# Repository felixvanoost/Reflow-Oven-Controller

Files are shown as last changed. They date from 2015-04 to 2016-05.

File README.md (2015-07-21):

Copyright Felix van Oost 2015.
This program is free software: you can redistribute it and/or modify it under the terms of the GNU General Public License as published by the Free Software Foundation, either version 3 of the License, or (at your option) any later version. This program is distributed in the hope that it will be useful, but WITHOUT ANY WARRANTY; without even the implied warranty of
MERCHANTABILITY or FITNESS FOR A PARTICULAR PURPOSE. See the GNU General Public License for more details.

# Reflow Oven Controller
A project to convert a standard toaster oven into a reflow soldering oven for PCB assembly using an Arduino and Python.

----------
Context
----------

The rapid adoption of surface-mount technology has revolutionised the electronics industry by reducing the size, cost, and power requirements of components. For the hobbyist, however, soldering these ever-smaller components by hand is becoming increasingly difficult. The most consistent and efficient way of soldering SMT components is by reflow soldering, a technique in which parts are attached to the PCB using solder paste and the entire board is then heated inside a purpose-built oven. The heat melts the solder paste, thereby permanently soldering the components to the board.

Reflow soldering requires precise control of the oven temperature, so the process is performed commercially in expensive, purpose-built reflow ovens. However, excellent results can be achieved on a budget by using a converted toaster oven and a microcontroller to monitor and adjust the temperature according to a specified thermal profile.

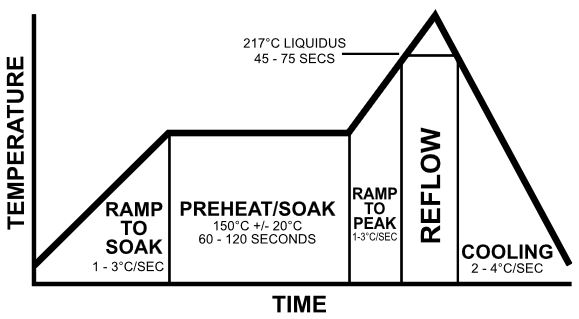
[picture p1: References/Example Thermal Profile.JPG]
Image of example thermal profile

*Example thermal profile*

The specific thermal profile followed by the microcontroller will depend on the type of solder paste and components used on the board (temperature guidelines are often provided in component datasheets). It is split into five main stages - ramp to soak, soak, ramp to reflow, reflow, and cooling. Each section dictates the specific temperature, time, and ramp up / down characteristics required for optimal soldering results. A full reflow cycle usually takes in the region of 4-6 minutes to complete.

----------
Overview
----------

This project consists of three main components:

- An off-the-shelf toaster oven fitted with a solid-state relay (SSR).
- An Arduino Uno to monitor and control the oven to follow a user-defined thermal profile.
- A Python script to provide a text-based UI for the Arduino and display a live plot of the oven temperature data on a computer.

To help keep the scope sufficiently narrow, I will assume that a suitable oven has been purchased and an SSR has already been installed within - there are a number of very good tutorials describing how to do this step-by-step. Information on choosing a suitable toaster oven for reflow soldering can be found [here](http://www.rocketscream.com/blog/2011/06/19/toaster-convection-or-infrared-oven/).

Four thermal profile parameters are user-configurable:

- Soak temperature
- Soak time
- Reflow temperature
- Reflow time

The Python script prompts the user to enter the desired values for each parameter, checks the input is within a pre-determined valid range, then sends the values to the Arduino via USB. Once the reflow cycle has been started, it receives an oven temperature reading from the Arduino every second and plots this on a graph for the user in real-time. The script also notifies the user when the cycle is complete or has been stopped for some reason.

The Arduino uses a finite state machine to implement the control logic, with a state corresponding to each stage in the reflow cycle. It controls the toaster oven using time-proportional control (a slower form of PWM). User feedback is provided via a set of LEDs and a buzzer.

----------
Hardware
----------

The hardware is split into the following main functional blocks:

- A thermocouple to measure the temperature inside the oven
- An amplifier circuit to amplify the voltage across the thermocouple to a level readable by the Arduino
- A temperature sensor to perform cold-junction compensation on the thermocouple temperature reading
- Pushbuttons to allow the user to start / stop the reflow process and implement any additional functionality
- LEDs and a buzzer to provide user feedback on the current stage in the reflow cycle

The following components are used:

- Arduino Uno or equivalent
- Arduino Proto Shield or equivalent
- K-type thermocouple wire (must be rated for at least 300C)
- Texas Instruments LM35Z Temperature Sensor
- Analog Devices OP07 Op-Amp or equivalent
- Texas Instruments LMC7660 Voltage Converter or equivalent (provides +/-5V bipolar output for the op-amp)
- Buzzer (this project uses a TDK PS1420P02CT)
- 4-Position screw terminal block
- 2x 8-DIP sockets
- 3x Pushbuttons (1 for start / stop, others for future additional functionality)
- 2x 5mm LEDs
- 2x 10µF electrolytic capacitors
- 2x 100Ω resistors
- 2x 330Ω resistors
- 3x 10kΩ resistors
- 2x 47kΩ resistors

The OP07 was chosen for its low input voltage characteristics (as the thermocouple produces an output voltage on the order of microvolts), although any op-amp with similar specifications will work just fine. The same is true for the LMC7660 - any voltage converter providing a +/-5V output from a 5V input can be used.

I decided to mount the hardware on an [OSEPP Proto Shield](http://osepp.com/products/shield-arduino-compatible/proto-shield/) (functionally identical to the [Sparkfun ProtoShield Kit](https://www.sparkfun.com/products/7914)), which comes pre-installed with a pushbutton and two LEDs. This reduces the number of components that need to be soldered to the board and simplifies the layout and assembly process. A full hardware schematic is provided in the 'Hardware' folder, and a few photos of the completed shield (one of many possible board layouts) can be found in the 'Photos' folder.

----------
Software
----------

The following software is required:

- Arduino IDE (latest version preferred)
- Python 3.4.2 (I opted to use IDLE in [WinPython](http://winpython.github.io/) 3.4.3.3 to run the Python UI script)

Further information about software / firmware setup and a detailed overview of the control logic is provided with each major release in the 'releases' section. Releases are versioned in the form vX.Y.ZZ, where X indicates a major new release, Y indicates a minor feature addition / update, and ZZ denotes a simple bug fix.

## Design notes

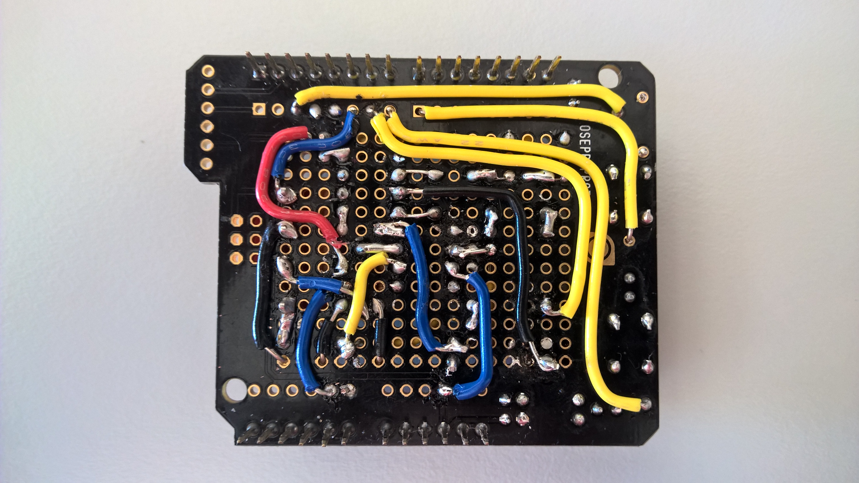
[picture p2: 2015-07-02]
Photos/Reflow Oven Controller 3.jpg

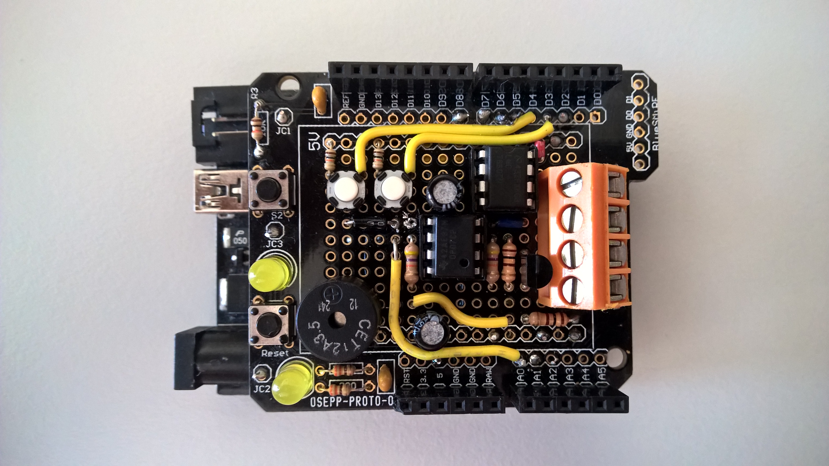
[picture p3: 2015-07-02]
Photos/Reflow Oven Controller 2.jpg

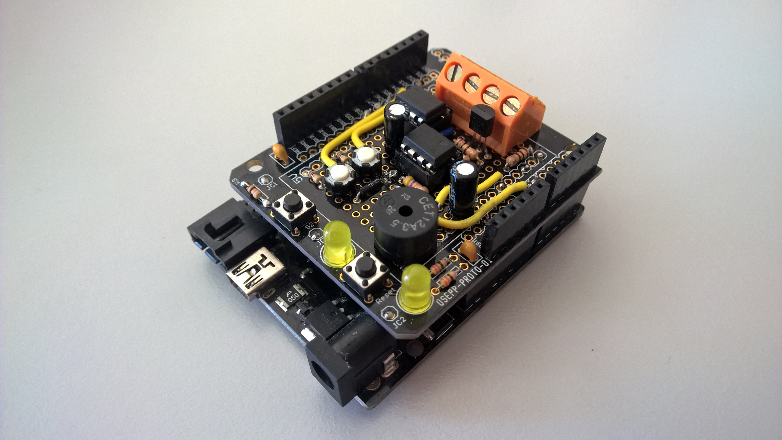
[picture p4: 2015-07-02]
Photos/Reflow Oven Controller 1.jpg

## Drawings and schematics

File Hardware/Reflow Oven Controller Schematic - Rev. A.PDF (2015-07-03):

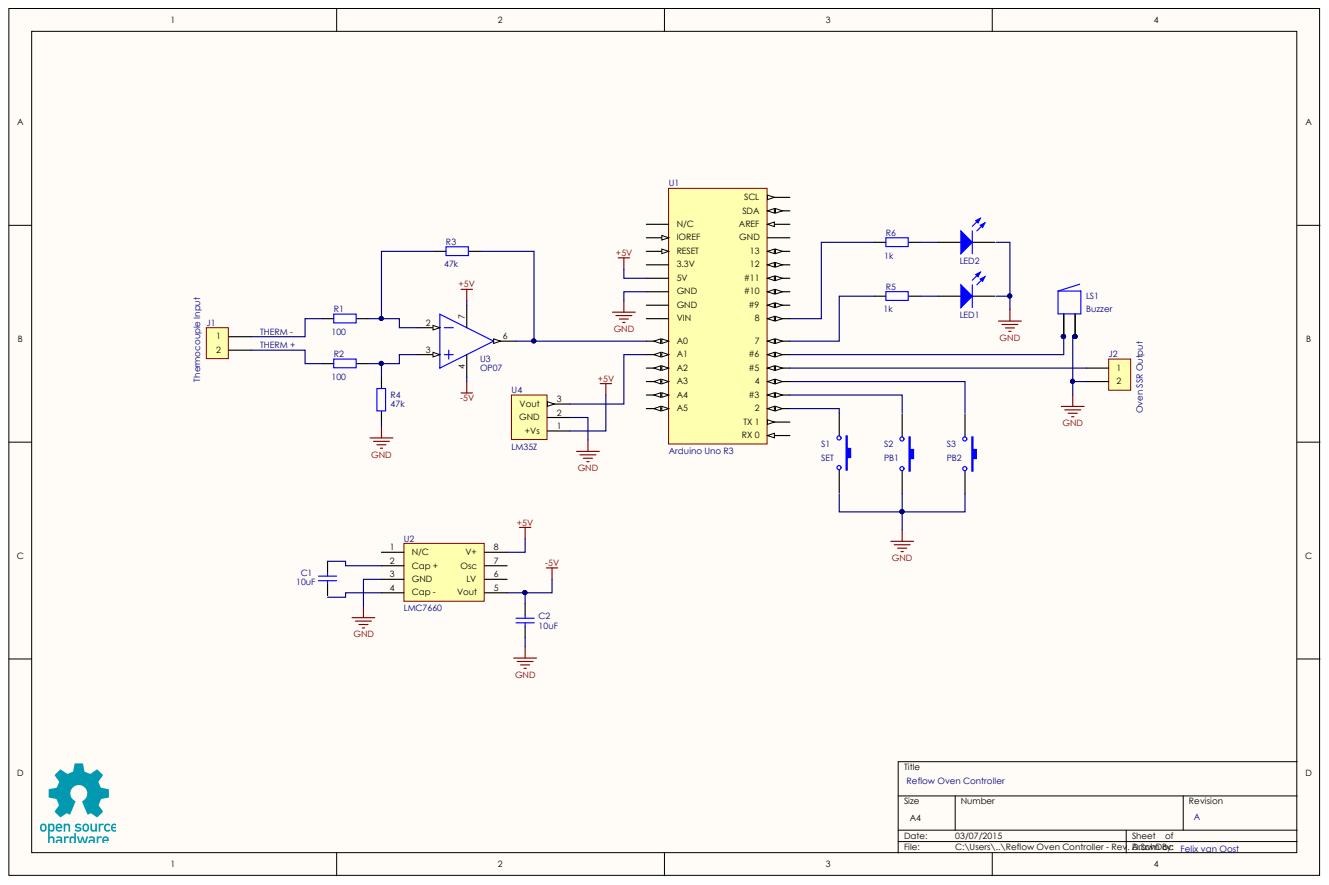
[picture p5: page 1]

S ize A4 | Num ber | Rev ision A

Date: 0 3/0 7/2 0 1 5 | Sheet of
Fi le: C :\Users\. .\Reflow Oven Control ler - Rev | . A. DraSchDoc wn By: Fel ix v an Oost

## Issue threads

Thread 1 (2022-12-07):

ISR bloated

eda1-fiunam, 2022-12-07:
I've just discovered your project, congrats! It seems very interesting, although I don't know yet whether it works, but I guess so. The first thing I've noted is that you've placed a very intensive floating point math inside the ISR. Good programming practices say that one shouldn't bloat an ISR, but delegates the user code to a regular function. I'm working on a similar project but using Fuzzy logic and a 32-bit Cortex ARM microcontroller. I'm in the design phase, and when it's time to build the electronics I'll check your project out thoroughly (I have no doubts about its performance) because it's a gold mine. Greetings.

FelixVanOost, 2022-12-09:
Hey @eda1-fiunam, thanks for getting in touch! I'm glad to hear that you found the project interesting.

I wrote this code a long time ago as a student and would do things quite differently today. You're correct in saying that ISRs should be kept as short as possible to avoid scheduling issues when multiple tasks are operating. This isn't always an issue if the ISR is the only code being executed though, or if the background code that the ISR has higher priority over doesn't need to run at a fixed period (which is somewhat true of the state machine that's running in the `loop()` function here).

In terms of execution time, the arithmetic in the ISR is trivial on any modern microcontroller with an FPU. The slowest functions are probably `Serial.print()` and the 1D look-up `pgm_read_word_near()`.

Good luck and happy hacking!

Felix

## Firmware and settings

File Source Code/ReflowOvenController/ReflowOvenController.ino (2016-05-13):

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
// Reflow Oven Controller v2.0.00

#include <avr/pgmspace.h>

// Analog pin definitions
#define thermPin                     A0                                       // Thermocouple input pin (A0)
#define junctionPin                  A1                                       // Cold junction input pin (A1)

// Digital pin definitions
#define setButtonPin                 2                                        // Pushbutton input pins (D2-D4)
#define Button1Pin                   3
#define Button2Pin                   4
#define ovenPin                      5                                        // Oven SSR pin (D5)
#define buzzerPin                    6                                        // Buzzer output pin (D6)
#define LED1Pin                      7                                        // LED output pins (D7-D8)
#define ovenLEDPin                   8

#define DEBOUNCE_DELAY               50                                       // Pushbutton debounce delay (ms)

// Buzzer frequencies (Hz)
#define LOW_BUZZER_FREQ              3000
#define MID_BUZZER_FREQ              4000
#define HIGH_BUZZER_FREQ             5000

// Buzzer beep lengths (ms)
#define SHORT_BEEP                   100
#define MEDIUM_BEEP                  400
#define LONG_BEEP                    3000

// Finite-state machine states
#define OFF                          0
#define RAMP_TO_SOAK                 1
#define SOAK                         2
#define RAMP_TO_REFLOW               3
#define REFLOW                       4
#define COOLING                      5

// PID coefficients
#define Kp                           12
#define Ki                           0
#define Kd                           3

// Oven temperature reading array size
#define READING_ARRAY_SIZE           10

// Oven temperature error array size
#define ERROR_ARRAY_SIZE             3

#define ERROR_TEMP                   35                                       // Thermocouple error temperature threshold (stops reflow process if not reached within the first 30 seconds)
#define SAFE_TO_HANDLE_TEMP          60                                       // Safe-to-handle temperature

byte state = OFF;

struct thermalProfile
{
  byte soakTemp;
  byte soakTime;
  byte reflowTemp;
  byte reflowTime;
};
typedef struct thermalProfile thermalProfile;                                 // Create a thermal profile structure
thermalProfile custom;

volatile float TargetTemp = 0;
volatile float OvenTempReading[READING_ARRAY_SIZE];
volatile float OvenTemp = 0;
volatile float OvenTempError[ERROR_ARRAY_SIZE];
volatile float TotalTempError = 0;
volatile float DeltaTemp = 0;
volatile float OvenOutput = 0;

volatile unsigned int cycleTime = 0;
volatile unsigned int stateTime = 0;

volatile byte interruptCount = 0;

// 0-255C LUT for K-type thermocouple in mV (stored in program memory)
const int thermLUT[] PROGMEM = {0,    18,   37,   56,   74,   93,   112,  130,  149,  168,
                                187,  205,  224,  243,  262,  281,  299,  318,  337,  356,
                                375,  394,  413,  432,  451,  470,  489,  508,  527,  547,
                                565,  585,  604,  623,  642,  661,  681,  700,  719,  738,
                                758,  777,  796,  815,  835,  854,  873,  893,  912,  932,
                                951,  970,  990,  1009, 1028, 1048, 1067, 1087, 1106, 1126,
                                1145, 1165, 1184, 1204, 1223, 1243, 1262, 1282, 1301, 1321,
                                1340, 1360, 1379, 1399, 1418, 1438, 1457, 1477, 1496, 1516,
                                1535, 1555, 1575, 1594, 1614, 1633, 1653, 1672, 1692, 1711,
                                1731, 1750, 1770, 1789, 1809, 1828, 1848, 1867, 1886, 1906,
                                1925, 1945, 1964, 1983, 2003, 2022, 2042, 2061, 2081, 2100,
                                2119, 2139, 2158, 2178, 2197, 2216, 2235, 2255, 2274, 2293,
                                2312, 2332, 2351, 2370, 2389, 2408, 2428, 2447, 2466, 2485,
                                2504, 2523, 2543, 2562, 2581, 2600, 2619, 2638, 2657, 2676,
                                2695, 2714, 2733, 2752, 2771, 2790, 2809, 2828, 2847, 2866,
                                2885, 2904, 2923, 2942, 2961, 2979, 2999, 3017, 3036, 3055,
                                3074, 3093, 3111, 3130, 3149, 3168, 3187, 3206, 3225, 3243,
                                3262, 3281, 3300, 3318, 3337, 3356, 3375, 3393, 3412, 3431,
                                3450, 3469, 3487, 3506, 3525, 3544, 3562, 3581, 3600, 3619,
                                3637, 3656, 3675, 3694, 3713, 3731, 3750, 3769, 3788, 3807,
                                3825, 3844, 3862, 3881, 3900, 3919, 3938, 3956, 3975, 3995,
                                4013, 4032, 4051, 4070, 4089, 4107, 4126, 4145, 4164, 4183,
                                4202, 4221, 4239, 4259, 4277, 4296, 4315, 4334, 4353, 4372,
                                4391, 4410, 4429, 4448, 4467, 4486, 4505, 4524, 4543, 4562,
                                4581, 4600, 4619, 4638, 4657, 4677, 4696, 4715, 4734, 4753,
                                4772, 4791, 4810, 4830, 4849, 4868};

void setup() 
{
  pinMode(thermPin, INPUT);
  pinMode(junctionPin, INPUT);
  pinMode(setButtonPin, INPUT_PULLUP);                                        // Enable internal pull-up resistors on pushbutton pins
  pinMode(Button1Pin, INPUT_PULLUP);
  pinMode(Button2Pin, INPUT_PULLUP);
  pinMode(ovenPin, OUTPUT);
  pinMode(buzzerPin, OUTPUT);
  pinMode(LED1Pin, OUTPUT);
  pinMode(ovenLEDPin, OUTPUT);

  // Turn LEDS off
  digitalWrite(LED1Pin, 0);
  digitalWrite(ovenLEDPin, 0);

  // Initialise oven temperature reading array to 20 (average room temperature)
  for(byte i = 0; i < READING_ARRAY_SIZE; i++)
  {
    OvenTempReading[i] = 20;
  }

  // Initialise oven temperature error array to 0
  for(byte i = 0; i < ERROR_ARRAY_SIZE; i++)
  {
    OvenTempError[i] = 0;
  }

  // Initialise serial port at 9600 baud
  Serial.begin(9600);
}

// Description:    Obtains an analog reading for the cold junction from the LM35Z and converts it to a temperature in Celsius.
// Parameters:    -
// Returns:       A temperature reading for the cold junction in Celsius.
byte getJunctionTemp()
{
  double junctionReading = 0;
  
  junctionReading = analogRead(junctionPin);                                  // Obtain 10-bit cold junction reading from the ADC
  junctionReading = ((junctionReading * 5.0 * 100.0) / 1023.0);               // Convert reading to temperature in Celsius
  
  return byte(junctionReading);
}

// Description:   Obtains an analog reading for the thermcouple and converts it to a temperature in Celsius using a LUT.
// Parameters:    -
// Returns:       A temperature reading for the thermocouple in Celsius.
byte getThermTemp()
{
  double thermReading = 0;
  byte i = 0;
  
  thermReading = analogRead(thermPin);                                        // Obtain 10-bit thermocouple reading from the ADC
  thermReading = ((thermReading * 5.0 * 1000.0) / 1023.0);                    // Convert reading to voltage (in mV)
  
  while(int(thermReading) > pgm_read_word_near(thermLUT + i))                 // Iterate through LUT to find the entry closest to the reading voltage
  {
    i++;
  }
  
  return i;                                                                   // Index of the LUT entry closest to the reading voltage is the temperature in Celsius
}

// Description:   CTC Interrupt Service Routine for Timer 1
//                1. Obtains oven temperature readings at 5Hz and stores the last READING_ARRAY_SIZE readings in an array
//                2. Calculates the proportional, intergral, and derivative terms for the PID loop
//                3. Increments the total cycle time and state time every second
//                4. Sends the current oven temperature to Python
//                5. Controls the oven using a slow form of PWM (due to switching speed limitations of the SSR)
ISR(TIMER1_COMPA_vect)
{
  byte i = 0;
  
  interruptCount++;

  // Execute at 5Hz
  if(interruptCount == 20)
  {
    // Shift temperature reading array values by one entry
    for(i = READING_ARRAY_SIZE - 1; i > 0; i--)
    {
      OvenTempReading[i] = OvenTempReading[i - 1];
    }
    
    // Obtain the latest oven temperature reading by adding together the thermocouple and cold junction readings
    OvenTempReading[0] = getThermTemp() + getJunctionTemp();

    // Calculate new average oven temperature
    OvenTemp = 0;
    
    for(i = 0; i < READING_ARRAY_SIZE; i++)
    {
      OvenTemp += OvenTempReading[i];
    }
    
    OvenTemp = OvenTemp / READING_ARRAY_SIZE;
    
    // Shift error array values by one entry
    for(i = ERROR_ARRAY_SIZE - 1; i > 0; i--)
    {
      OvenTempError[i] = OvenTempError[i - 1];
    }

    // Calculate and store new error value
    OvenTempError[0] = TargetTemp - OvenTemp;
    
    // Calculate new total error value
    TotalTempError += OvenTempError[0];

    // Calculate new derivative value
    DeltaTemp = (OvenTempError[0] - OvenTempError[ERROR_ARRAY_SIZE - 1]) / (ERROR_ARRAY_SIZE * 0.01);
    
    // Calculate output value
    OvenOutput = (OvenTempError[0] * Kp) + (TotalTempError * Ki) + (DeltaTemp * Kd);
    OvenOutput = int(constrain(OvenOutput, 0, 100));
  }

  // Execute every second
  else if(interruptCount == 100)
  {
    // Increment cycle and state time
    cycleTime++;
    stateTime++;

    // Send current oven temperature to Python
    Serial.print(int(OvenTemp));
    Serial.print("\n");

    interruptCount = 0;
  }

  if(TargetTemp = 0)
  {
    OvenOutput = 0;
  }

  // Control oven using slow form of PWM (off if unterruptCount > OvenOutput, on otherwise)
  digitalWrite(ovenPin, interruptCount > OvenOutput ? 0:1);
  digitalWrite(ovenLEDPin, interruptCount > OvenOutput ? 0:1);                // Toggle oven LED to mirror oven state
}

// Description:   Initialises Timer 1 to interrupt every 10ms.
// Parameters:    -
// Returns:       -
void initialiseTimer1()
{
  cli();                                                                      // Disable global interrupts
  TCCR1A = 0;                                                                 // Reset Timer 1 configuration registers
  TCCR1B = 0;
  TCNT1 = 0;                                                                  // Load Timer 1 with 0
  OCR1A = 0x4E1F;                                                             // Load output compare register with 19,999 to create a compare match interrupt every 10ms
  TIMSK1 |= (1 << OCIE1A);                                                    // Enable Timer 1 CTC (Clear Timer on Compare) interrupt
  TCCR1B |= (1 << WGM12);                                                     // Select CTC mode
  TCCR1B |= (1 << CS11);                                                      // Select internal 16MHz oscillator with CLK / 8 prescaling as clock source and start Timer 1
  sei();                                                                      // Enable global interrupts
}

// Description:   1. Receives a thermal profile parameter from Python via the serial port
//                2. Echoes the received value back to Python to ensure that the correct data has been received
//                3. Provides user feedback via the buzzer
// Parameters:    -
// Returns:       The value of the received thermal profile parameter
int receiveParameter()
{
  int value = 0;
  
  while(value == 0)
  {
    if(Serial.available() > 0)                                                // Check if data has arrived in the serial receive buffer
    {
      value = Serial.parseInt();                                              // Read data from the buffer and convert to an integer
      Serial.print(value);                                                    // Echo received value back to Python
      Serial.print("\n");
    }
  }
  tone(buzzerPin, HIGH_BUZZER_FREQ, SHORT_BEEP);
  
  return byte(value);
}

void loop()
{
  // Finite-state machine control logic
  switch(state)
  {
    // Idle state
    case OFF:
    {
      cycleTime = 0;
      digitalWrite(LED1Pin, 0);
      TCCR1B = 0;                                                             // Stop Timer 1

      // Obtain thermal profile parameters
      custom.soakTemp = receiveParameter();
      custom.soakTime = receiveParameter();
      custom.reflowTemp = receiveParameter();
      custom.reflowTime = receiveParameter();

      // Wait for 'set' button to be pressed to begin the reflow process
      while(digitalRead(setButtonPin) != 0);
      while(digitalRead(setButtonPin) == 0);                                  // Wait for 'set' button to be released      
      delay(DEBOUNCE_DELAY);
      digitalWrite(LED1Pin, 1);
      Serial.print("Start\n");                                                // Send 'start' flag to Python

      // Play start melody
      tone(buzzerPin, LOW_BUZZER_FREQ, MEDIUM_BEEP);
      delay(SHORT_BEEP);
      tone(buzzerPin, MID_BUZZER_FREQ, MEDIUM_BEEP);
      delay(SHORT_BEEP);
      tone(buzzerPin, HIGH_BUZZER_FREQ, MEDIUM_BEEP);
     
      initialiseTimer1();
      stateTime = 0;
      state = RAMP_TO_SOAK;
      break;
    }
    // Ramp to soak state
    case RAMP_TO_SOAK:
    { 
      TargetTemp = custom.soakTemp;

      // Stop reflow process if 'set' button is pressed
      if(digitalRead(setButtonPin) == 0)
      {
        while(digitalRead(setButtonPin) == 0);                                // Wait for 'set' button to be released
        delay(DEBOUNCE_DELAY);
        TargetTemp = 0;
        Serial.print("Stop\n");                                               // Send 'stop' flag to Python
        delay(20);                                                            // Ensure Timer 1 ISR is given enough time to execute and turn off the oven before returning to Idle state
        state = OFF;
        break;
      }
      if(stateTime == 30 && OvenTemp < ERROR_TEMP)                            // Stop reflow process if oven does not reach the specified error temperature in the first 30s (thermocouple error)
      {
        TargetTemp = 0;
        Serial.print("Therm\n");                                              // Send 'thermocouple error' flag to Python
        delay(20);                                                            // Ensure Timer 1 ISR is given enough time to execute and turn off the oven before returning to Idle state
        state = OFF;
        break;
      }
      // Enter soak state once soak temperature has been reached
      if(OvenTemp > custom.soakTemp)
      {
        stateTime = 0;
        tone(buzzerPin, MID_BUZZER_FREQ, MEDIUM_BEEP);
        state = SOAK;
      }
      break;
    }
    // Soak state
    case SOAK:
    {
      TargetTemp = custom.soakTemp;
      
      // Stop reflow process if 'set' button is pressed
      if(digitalRead(setButtonPin) == 0)
      {
        while(digitalRead(setButtonPin) == 0);                                // Wait for 'set' button to be released
        delay(DEBOUNCE_DELAY);
        TargetTemp = 0;
        Serial.print("Stop\n");                                               // Send 'stop' flag to Python
        delay(20);                                                            // Ensure Timer 1 ISR is given enough time to execute and turn off the oven before returning to Idle state
        state = OFF;
        break;
      }
      // Enter ramp to reflow state once soak time has elapsed
      if(stateTime == custom.soakTime)
      {
        stateTime = 0;
        tone(buzzerPin, MID_BUZZER_FREQ, MEDIUM_BEEP);
        state = RAMP_TO_REFLOW;
      }
      break;
    }
    // Ramp to reflow state
    case RAMP_TO_REFLOW:
    {
      TargetTemp = custom.reflowTemp;

      // Stop reflow process if 'set' button is pressed
      if(digitalRead(setButtonPin) == 0)
      {
        while(digitalRead(setButtonPin) == 0);                                // Wait for 'set' button to be released
        delay(DEBOUNCE_DELAY);
        TargetTemp = 0;
        Serial.print("Stop\n");                                               // Send 'stop' flag to Python
        delay(20);                                                            // Ensure Timer 1 ISR is given enough time to execute and turn off the oven before returning to Idle state
        state = OFF;
        break;
      }
      // Enter reflow state once reflow temperature has been reached
      if(OvenTemp > custom.reflowTemp)
      {
        stateTime = 0;
        tone(buzzerPin, MID_BUZZER_FREQ, MEDIUM_BEEP);
        state = REFLOW;
      }
      break;
    }
    // Reflow state
    case REFLOW:
    {
      TargetTemp = custom.reflowTemp;

      // Stop reflow process if 'set' button is pressed
      if(digitalRead(setButtonPin) == 0)
      {
        while(digitalRead(setButtonPin) == 0);                                // Wait for 'set' button to be released
        delay(DEBOUNCE_DELAY);
        TargetTemp = 0;
        Serial.print("Stop\n");                                               // Send 'stop' flag to Python
        delay(20);                                                            // Ensure Timer 1 ISR is given enough time to execute and turn off the oven before returning to Idle state
        state = OFF;
        break;
      }
      // Enter cooling state once reflow time has elapsed
      if(stateTime == custom.reflowTime)
      {
        stateTime = 0;
        TargetTemp = 0;
        tone(buzzerPin, MID_BUZZER_FREQ, LONG_BEEP);                          // Alert user to open oven door
        state = COOLING;
      }
      break;
    }
    // Cooling state
    case COOLING:
    {
      if(OvenTemp < SAFE_TO_HANDLE_TEMP)                                      // Finish reflow process once safe-to-handle temperature is reached
      {
        stateTime = 0;
        TCCR1B = 0;                                                           // Stop Timer 1
        
        digitalWrite(LED1Pin, 0);
        Serial.print("Done\n");                                               // Send 'done' flag to Python

        // Play end melody
        tone(buzzerPin, HIGH_BUZZER_FREQ, MEDIUM_BEEP);
        delay(SHORT_BEEP);
        tone(buzzerPin, MID_BUZZER_FREQ, MEDIUM_BEEP);
        delay(SHORT_BEEP);
        tone(buzzerPin, LOW_BUZZER_FREQ, MEDIUM_BEEP);
        
        Serial.print(cycleTime);                                              // Send total reflow cycle time to Python
        state = OFF;
      }
      break;
    }
  }
}

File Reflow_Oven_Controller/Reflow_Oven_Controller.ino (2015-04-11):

// Reflow Oven Controller Shield for the Arduino
// v1.0, Built 10/04/2015

void setup() 
{
  #define THERM        0                                         // Define thermocouple input pin (A0)
  #define JUNCTION     1                                         // Define cold junction input pin (A1)
  
  #define SETBUTTON    2                                         // Define pushbutton input pins (D2-D4)
  #define INCBUTTON    3
  #define DECBUTTON    4
  #define STATE1LED    5                                         // Define LED output pins (D5-D8)
  #define STATE2LED    6
  #define STATE3LED    7
  #define STATE4LED    8
  #define BUZZER       9                                         // Define buzzer output pin (D9)
  #define OVEN         10                                        // Define oven SSR pin (D10)
  
  pinMode(THERM, INPUT);                                         // Declare pins as inputs
  pinMode(JUNCTION, INPUT);
  pinMode(SETBUTTON, INPUT);
  pinMode(INCBUTTON, INPUT);
  pinMode(DECBUTTON, INPUT);
  
  pinMode(STATE1LED, OUTPUT);                                    // Declare pins as outputs
  pinMode(STATE2LED, OUTPUT);
  pinMode(STATE3LED, OUTPUT);
  pinMode(STATE4LED, OUTPUT);
  pinMode(BUZZER, OUTPUT);
  pinMode(OVEN, OUTPUT);
  
  Serial.begin(9600);                                            // Initialise serial port at 9600 baud
}

// Description:		Obtains an analog reading for the cold junction from the LM335 and converts it to a temperature in Celsius 
// Parameters:		-
// Returns:		The cold junction temperature in Celsius
int getJunctionTemp()
{
  int junctionReading = 0;
  int junctionTemp = 0;
  
  junctionReading = analogRead(JUNCTION);                        // Obtain 10-bit cold junction reading from the ADC
  junctionTemp = ((junctionReading / 1023) * 5 * 100) - 273;     // Convert reading to temperature in Celsius
  return junctionTemp;
}

void loop() 
{
  // FOR DEBUGGING
  int junctionTemp = 0;
  junctionTemp = getJunctionTemp();
  Serial.println(junctionTemp);
  delay(1000);
}

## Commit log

2015-04-11 Defined I/O pin assignments and added pin declarations
2015-04-15 Modified getJunctionTemp function for LM35 sensor
    Function fully tested and debugged
2015-04-15 Added FSM shell functions and buzzer feedback when setting parameters
    [ReflowOvenController.ino]
2015-04-17 Changed ADC reference voltage and reduced memory requirements for variables
2015-04-21 Added overflow ISR for Timer 1
2015-04-21 Added stop and thermocouple error code
    [ReflowOvenController.ino]
2015-04-23 Added Excel file with thermocouple LUT calculations
    [K-type Thermocouple LUT.xlsx]
2015-04-30 Defined oven PWM duty cycle constants
2015-05-01 Minor changes to buzzer feedback
    [ReflowOvenController.ino]
2015-05-01 Added Python temperature graph script
2015-05-19 Reduced PWM frequency for oven SSR output
2015-05-20 Enabled internal pull-up resistors for pushbuttons
2015-05-26 Added bit-bang slow PWM control for oven
2015-05-26 Improved code efficiency for obtaining temperature readings
2015-05-26 Added moving average filter to temperature readings
2015-05-26 Made minor changes to moving average filter code
2015-05-26 Added functionality to LED1 (shows cycle is active)
2015-05-26 Fixed error in loop obtaining temperature readings
    [ReflowOvenController.ino]
2015-05-26 Modified Timer 1 to operate in CTC mode
2015-06-16 Added oven control and error handling improvements
    [ReflowOvenController.ino, ReflowOvenControllerUI.py]
2015-06-17 Added Rev. A Altium Designer Files
    [Reflow Oven Controller - Rev. A.PrjPcb, Reflow Oven Controller - Rev. A.SchDoc, Reflow Oven Controller - Rev. A.SchLib]
2015-07-02 Added photos of completed Arduino shield
2015-07-02 Implemented true moving average for temperature readings
2015-07-03 Added PDF of Rev. A hardware schematic
    [Reflow Oven Controller - Rev. A.PrjPcb, Reflow Oven Controller - Rev. A.SchDoc]
2016-04-26 [Arduino] Add PID oven control
2016-05-04 [Arduino] Fix temperature reading overflow issue
    [ReflowOvenControllerUI.py]
2016-05-13 [Arduino] Add moving average filter for PID control

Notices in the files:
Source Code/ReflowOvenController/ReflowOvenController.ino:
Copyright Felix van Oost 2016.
